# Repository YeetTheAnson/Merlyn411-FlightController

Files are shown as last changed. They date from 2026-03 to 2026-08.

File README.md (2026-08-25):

# Merlyn411 Flight Controller

> [!TIP]
> The Merlyn411 is outdated! Check out the [Merlyn435](https://github.com/YeetTheAnson/Merlyn435-Flight-Stack/) for a more powerful and modern flight controller + ESC.

## Introduction

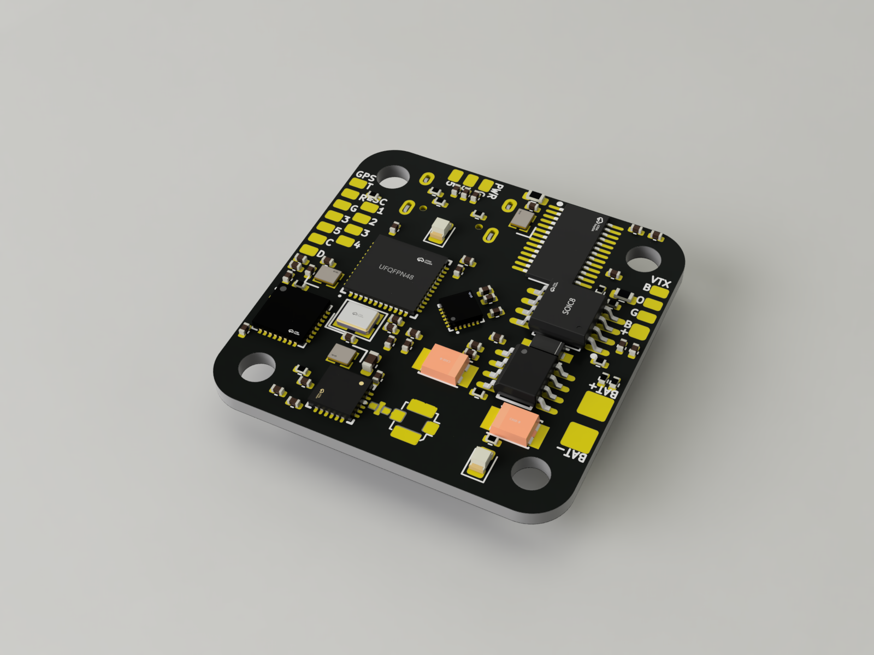
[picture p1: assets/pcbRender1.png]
render

This is my custom AIO (No ESC) flight controller! I started this project because commercial flight controllers get very expensive very quickly as you demand for more features like integrated radio receivers. I took on the challenge of designing my own betaflight compatible flight controller and it was difficult especially since the board has only 2 layers to save as much cost as possible and it's also my first time working with RF in circuits.

This flight controller is designed for a wide range of drones from 2" to as big as you want it to, and supports battery voltage from 2s to 8s although it is recommended to use a maximum of 6s. The 25.5mm pattern should be compatible with almost all frames on the market

It also features many quality of life features like an integrated ExpressLRS (ELRS) 2.4GHz receiver, an onboard OSD which inserts telemetry directly into the FPV video feed, 16MB flash memory for flight & blackbox logging and a buzzer for identifying error codes and to locate the drone.

While the primary focus of this projet is the flight controller hardware and firmware, I have also included a guide for the full 3 inch long range / freestyle drone build that this board was designed for

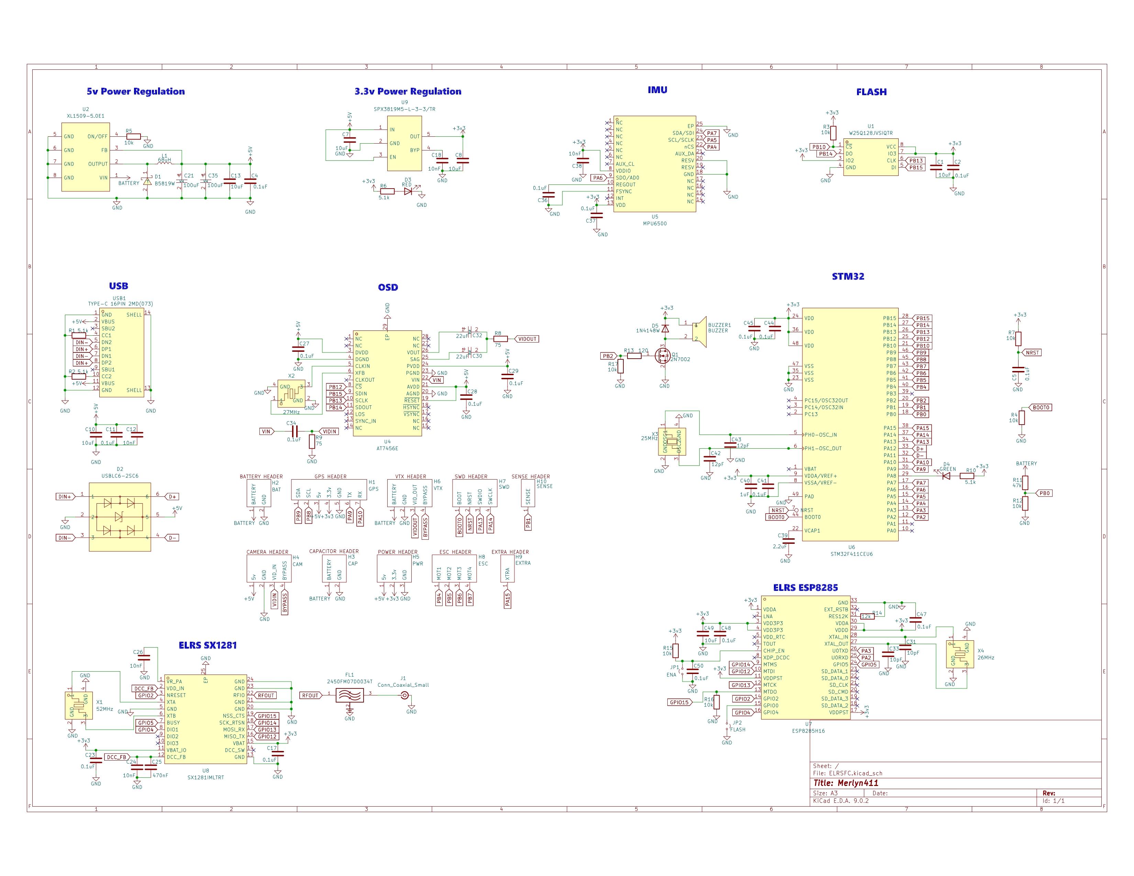
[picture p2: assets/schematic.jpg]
schematic

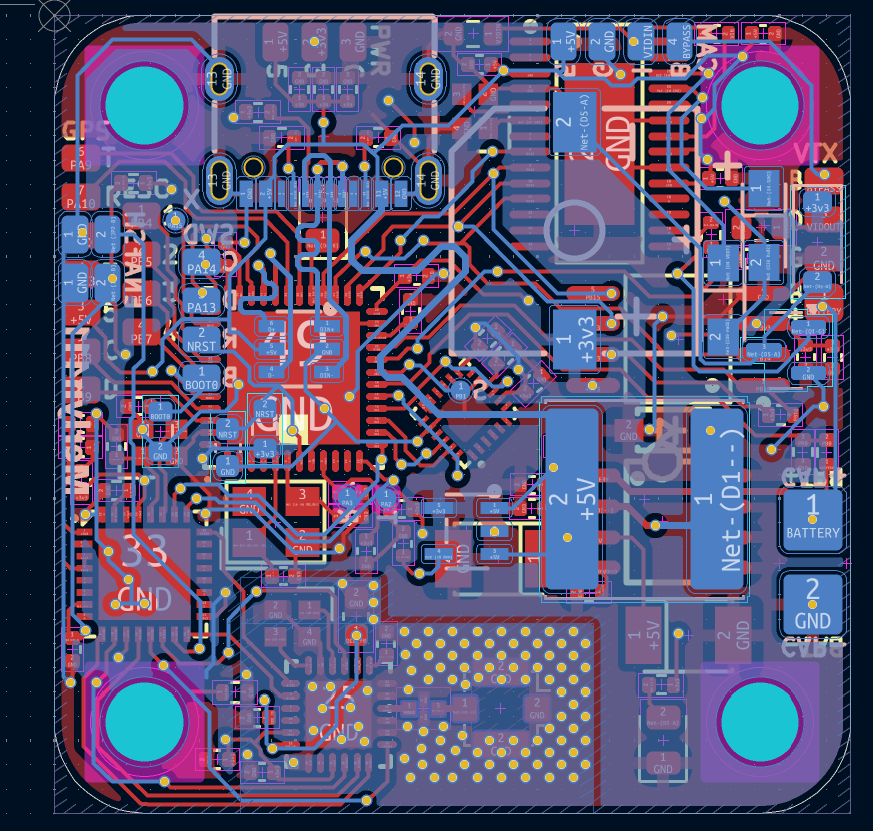
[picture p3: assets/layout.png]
layout

-----

## Hardware Specifications

  - **MCU:** STM32F411CEU6 (100MHz, 512KB Flash)
  - **IMU:** MPU6500 (SPI)
  - **OSD:** AT7456E (SPI)
  - **Blackbox:** Winbond W25Q128 16MB Flash (SPI)
  - **Receiver:** Integrated 2.4GHz ExpressLRS (ESP8285 & SX1281)
  - **Power Supply:** 5v and 3.3v rails up to 1A (3.3v rail is limited to 250mA)
  - **Mounting:** 25.5mm x 25.5mm square mounting pattern with M3 holes
  - **Peripherals** Includes pads for using external receivers, GPS, Magnetometer, analog camera and VTX

Note: The IMU should be in the forward facing direction if the USB C connector is facing forward and to the right. Adjust the mounting orientation accordingly in betaflight

-----

## Pinout
### External Headers

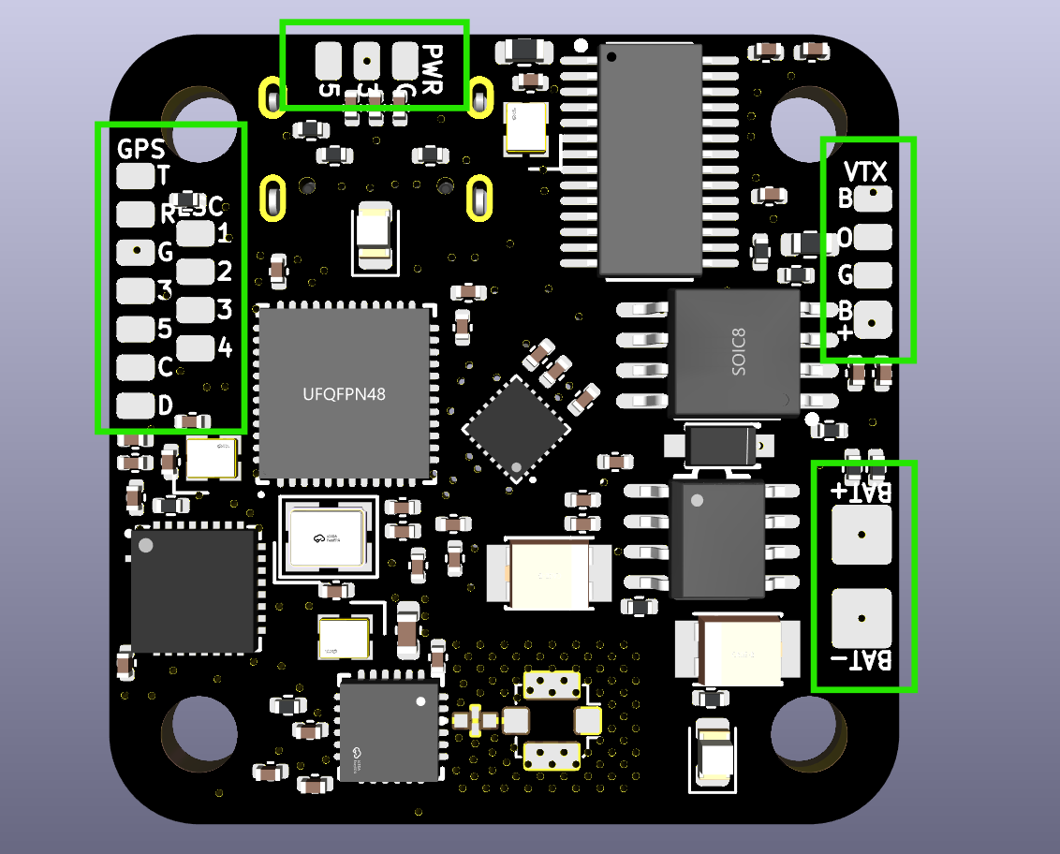
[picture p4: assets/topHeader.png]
topHeaders

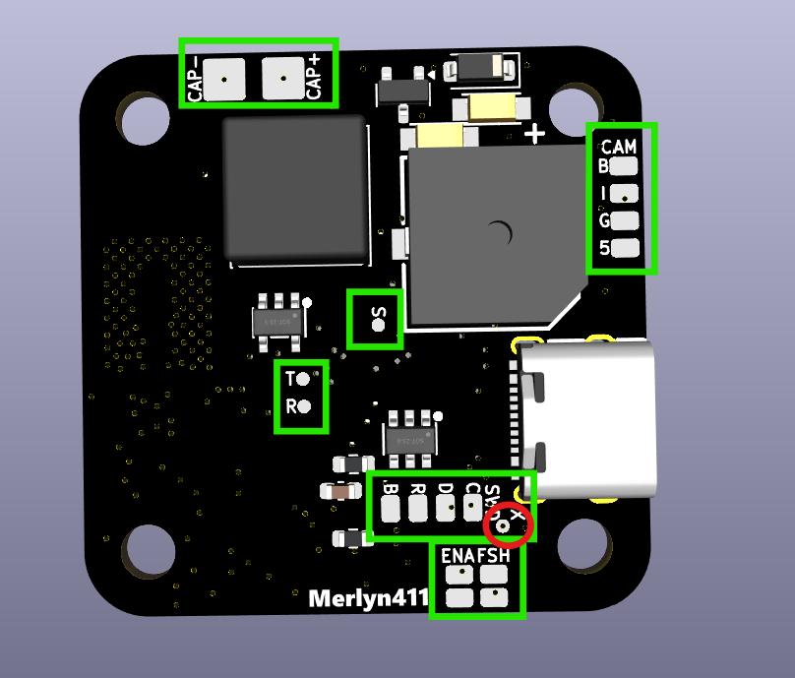
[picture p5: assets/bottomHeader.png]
bottomHeaders


| Header | Pin Name | STM32 Pin | Description |
| :--- | :--- | :--- | :--- |
| **GPS** | `T` | PA9 | UART1 TX (Connect to GPS RX) |
| | `R` | PA10 | UART1 RX (Connect to GPS TX) |
| | `3` | - | 3.3V Power Out |
| | `5` | - | 5V Power out |
| | `G` | - | Ground |
| | `C` | PB8 | I2C1 SCL (For Magnetometer) |
| | `D` | PB9 | I2C1 SDA (For Magnetometer) |
| **VTX** | `B`| - | Video Bypass (Direct from camera) |
| | `O` | - | Analog Video Out (From AT7456E) |
| | `G` | - | Ground |
| | `B+` | - | Battery Output |
| **CAM** | `B` | - | Video Bypass (Direct to VTX) |
| | `I` | - | Analog Video Input (From camera) |
| | `G` | - | Ground |
| | `5` | - | 5V Power Out |
| **SWD** | `C` | PA14 | SWCLK (Debug & Flash) |
| | `D` | PA13 | SWDIO (Debug & Flash) |
| | `R` | NRST | NRST (Debug & Flash) |
| | `B` | BOOT0 | BOOT0 (Debug & Flash) |
| **ESC** | `1-4` | PB4-PB7 | Motor Signal Outputs |
| **BAT** | `BAT+` | - | Battery Positive Input |
| | `BAT-` | - | Battery Negative Input |
| **CAP** | `CAP+` | - | Capacitor Anode |
| | `CAP-` | - | Capacitor Cathode |
| **PWR** | `G` | - | Ground |
| | `3` | - | 3.3V Power Out |
| | `5` | - | 5V Power Out |
| **Test Points** | `X` | PA15 | SmartAudio (Softserial 1 TX) |
| | `S` | PA15 | Current Sense Pin (From ESC) |
| | `T` | PA2 | ESP8285 RX Pin (STM32 TX PIN) |
| | `R` | PA3 | ESP8285 TX Pin (STM32 RX PIN) |

### Test Points & Pads

  - **External RX:**. Use these if you disable the internal ELRS receiver to connect other modules. Pad is labelled T and R on silkscreen.
  - **IRC Tramp and SmartAudio:** Connect VTX IRC or SmartAudio pin to the pad labeled with X on the silkscreen
  - **Current Sense:** Connect to ESC current sense pin. Pad is labelled S on silkscreen
  - **ENA & FSH:** Bridge ENA jumper to disable internal ELRS receiver. Bridge FSH jumper to put internal ELRS to flashing mode.
  - **Boot Mode (STM32):** To enter DFU mode for the flight controller, short the SWD B pad to any +3.3v rail while plugging in the USB.

-----

## Flight Controller Firmware (Betaflight)

Because this is a custom hardware layout, I believe that there is no standard targets that has the exact pin mapping as my flight controller. You must compile the firmware with the custom target definition in [/firmware/MERLYN411](https://github.com/YeetTheAnson/Merlyn411-FlightController/tree/main/firmware/MERLYN411) or use the pre compiled firmware in [/firmware/COMPILED](https://github.com/YeetTheAnson/Merlyn411-FlightController/tree/main/firmware/COMPILED).

> [!TIP]
> You can use flash another target to the flight controller and use betaflight CLI to remap the pin resource, however this is not recommended as the chosen target might not be compiled with a feature that this flight controller supports.

### How to build the firmware

1. Clone the [betaflight repository](https://github.com/betaflight/betaflight) using any UNIX terminal (use MYSYS2 MINGW64 on windows) and enter the directory
2. Enter `make configs` (install any required GCC toolchain if required)
3. Create a directory in betaflight/src/config/configs named `MERLYN411` and paste [config.h](https://github.com/YeetTheAnson/Merlyn411-FlightController/tree/main/firmware/MERLYN411/config.h) in the new directory
4. Enter `make MERLYN411` and the `.hex` file should appear in `betaflight/obj`

### Flashing the Flight Controller

1. **Via USB (DFU Mode):** Short the SWD `B` pad to 3.3v on the FC and plug in the USB C cable. Open Betaflight Configurator, select your compiled local `.hex` file, and click Flash Firmware.
2. **Via SWD:** If the bootloader is corrupted, connect an ST Link programmer to the `D`, `C`, and `D` (`R` is optional) pads and flash via STM32CubeProgrammer.

-----

## ExpressLRS Flashing

The internal ESP8285 and SX1281 receiver is wired to the STM32 via a hardware UART. It uses the standard **BETAFPV 2.4GHz Lite RX** firmware target. You can obtain the firmware binaries from the ELRS [site](https://expresslrs.github.io/web-flasher/) or from this repository in [/firmware/COMPILED](https://github.com/YeetTheAnson/Merlyn411-FlightController/tree/main/firmware/COMPILED). There's two way to flash the receiver:

### Method 1: Betaflight Passthrough

Note that betaflight must be installed and configured before passthrough works
1. Connect the FC via USB
2. Open the ExpressLRS Configurator [web flasher](https://expresslrs.github.io/web-flasher/) or app
3. Select `Receiver`
4. Select the `BETAFPV 2.4GHz Lite RX` target and press next
5. [OPTIONAL] Enter your bind phrase
6. Select the Betaflight Passthrough flashing method, press next and follow the steps

### Method 2: Manual Flashing

If the ESP8285 is bricked or passthrough fails, you can flash it directly using an FTDI adapter or another ESP8285/ESP8286/ESP32 or even an arduino

**Wiring the FTDI:**
The UART pads on the board are named relative to the STM32's perspective. Because the STM32's `TX` is connected to the ESP8285's `RX`, you must wire your FTDI adapter **RX to RX** and **TX to TX**.

  * FTDI `TX` -\> FC Pad `T`
  * FTDI `RX` -\> FC Pad `R`
  * FTDI `GND` -\> FC Pad `G`
  * FTDI `5V` -\> FC Pad `5` (or power via USB)

You must disable the STM32 when flashing via the T and R pad
using an external FTDI as it will intefere with the UART lines. You can disable the STM32 by shorting the SWD `R` pad to ground. Remember to short the `ENA` pads on the bottom side to put the ESP8285 into flashing mode.

-----

## Drone Assembly

While this project is mainly focused on the Merlyn411 flight controller, I designed it along with a high efficiency 3 inch cruiser drone in mind. If you want to recreate the full build, below is the component breakdown and assembly steps

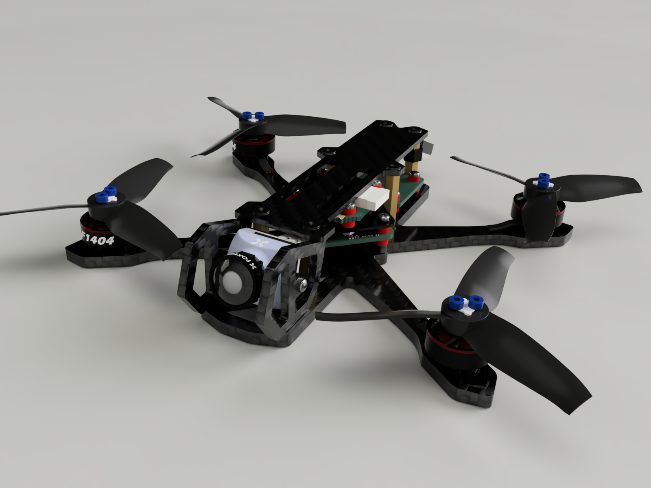
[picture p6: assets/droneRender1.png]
droneRender


### Component List
- **Flight Controller:** Merlyn411
- **ESC:** JHEMCU EM40A
- **Motors:** Sparkhobby 1303.5 5500KV
- **Propellers:** Gemfan 3016 Tri-Blade
- **VTX:** JHEMCU 600mW VTX
- **Camera:** Analog FPV micro(19mm) camera
- **Frame:** Custom frame
- **Battery:** 2S-4S LiPo or 2S/3S 18650 Li Ion packs

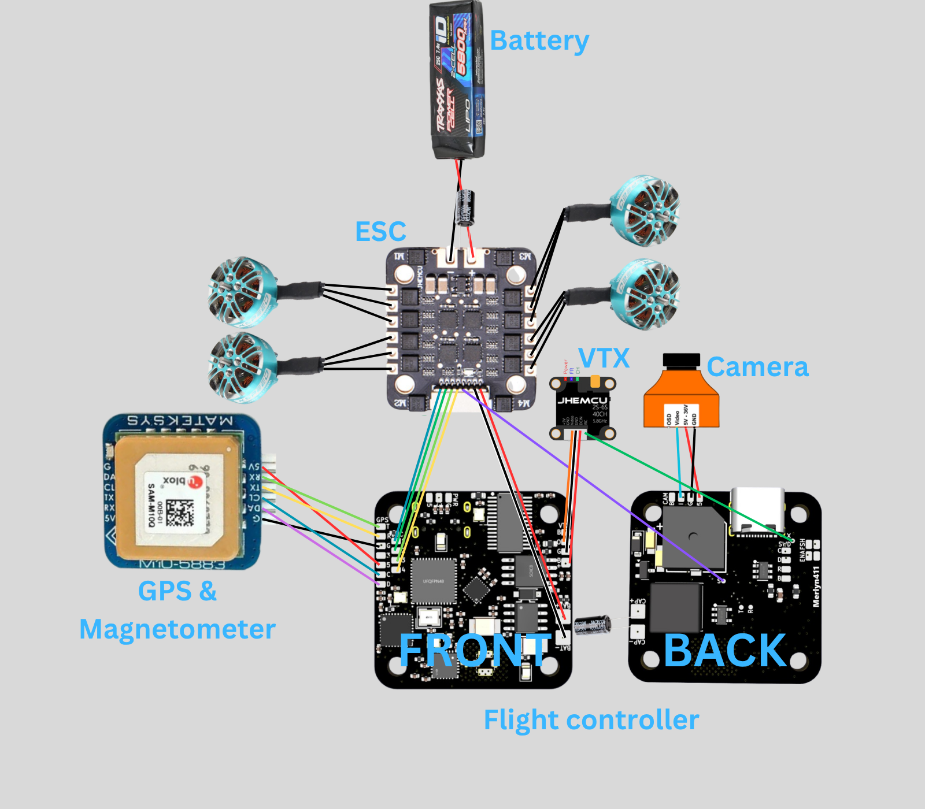
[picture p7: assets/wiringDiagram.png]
Wiring Diagram


### Why 3D Printing the Frame is Not Recommended
Currently, I am using a custom frame that I 3D printed for prototyping. I strongly advise against using a 3D printed frame for your final build. The Merlyn411 uses the MPU6500 IMU, which is sensitive to mechanical noise and vibrations. 3D printed frames will flex and resonate significantly more than carbon fiber frames. This flexing will send noise into the gyro and resulting in terrible flight performance. Also the 3D printed frame will likely not survive a moderate impact.

### Fasteners
Because this is a custom stack with a 25.5mm FC and a 20mm ESC, the stack up is very specific. You will need:
* 6x M3 20mm Female to Female Brass Standoffs (Frame separation)
* 12x M3 6mm Screws (Frame to standoffs)
* 4x M2 Nuts (Stack base)
* 4x M2 16mm Screws (Main stack skewers)
* 8x M2 10mm Screws (Top stack/VTX skewers)
* 16x M2 6mm Screws (Motors)
* 4x M2 6mm Screws (Camera/Props)

### FC Stack
The Merlyn411 uses a 25.5x25.5mm mounting pattern (which is meant for AIO boards). However, I needed a standalone ESC which comes in standard sizes like 20x20mm.

To make these fit together, you must use a 3D printed adapter plate in [/production/3dPrint/boardAdapter.stl](https://github.com/YeetTheAnson/Merlyn411-FlightController/blob/main/production/3dPrint/boardAdapter.stl). 

**Stack Assembly Layer 1:**
1.  Place 4x M2 Nuts into the designated recesses in the bottom frame plate.
2. Push rubber grommets into the flight controller
3. Push 4x M2 16mm screws through the adapter plate, through the rubber grommet, and through the bottom plate into the M2 nuts
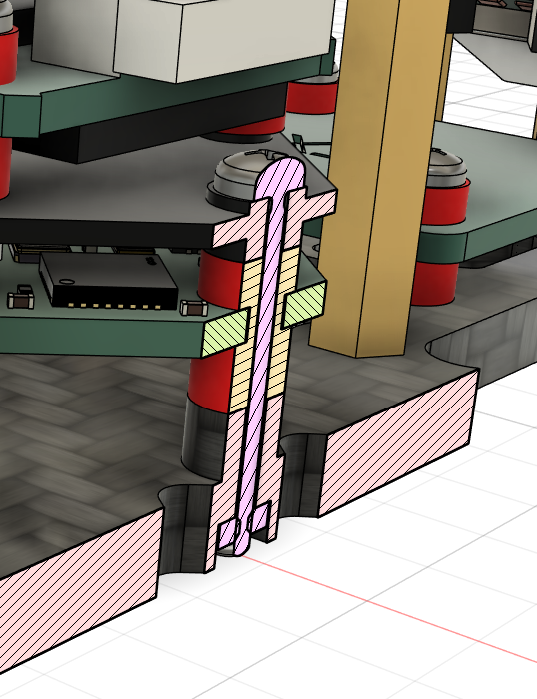
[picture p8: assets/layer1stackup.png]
layer1


**Stack Assembly Layer 2:**
1. Push rubber grommets into the ESC
2. Push 4x M2 10mm screws through rubber grommets and through the adapter plate until it reaches another set of M2 nuts
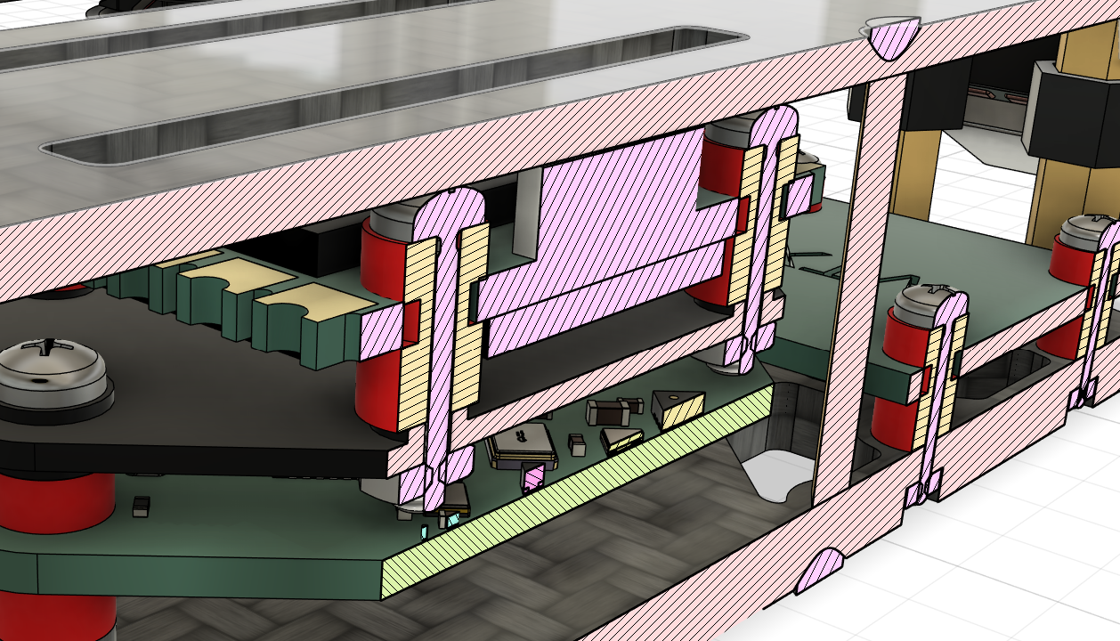
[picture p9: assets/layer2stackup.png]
layer2


### Mounting the VTX
The JHEMCU 600mW VTX mounts to the rear of the frame.
1.  Place 4x M2 Nuts into the bottom frame plate at in the rear
2. Push rubber grommets into the VTX
3.  Thread 4x M2 10mm screws through rubber grommets, down through the bottom plate, and into the nuts

### Final Assembly
1.  **Motors:** Mount the four 1303.5 5500KV motors to the arms using 16x M2 6mm screws (4 per motor). Ensure the screws do not touch the motor windings inside the bell.
2.  **Propellers:** Mount the Gemfan 3016 propeller. Pay attention to motor rotation directions (depending on your betaflight configuration, it could either be prop in or prop out). Fasten each prop with 2x M2 6mm screws.
3.  **Camera:** Mount the analog FPV camera to the front using 2x M2 6mm screws.
4.  **Closing the Frame:** Use the 6x M3 20mm standoffs and 12x M3 6mm screws to secure the top plate to the bottom plate

## Bill of Material
Note: The prices in USD are converted as of 31 March 2026 and prices may fluctuate. The requested funding is $200 as a buffer for the unstable prices. Any unused funds is returned.

| Item Name | Link | Vendor | Quantity | Total Price (USD) |
|---|---|---|---|---|
| 2450FM07D0034 | [Link](https://www.aliexpress.com/item/1005007939000699.html) | AliExpress | 1 | 6.40 |
| AliExpress Shipping |  | AliExpress | 1 | 3.15 |
| PCB |  | JLCPCB | 1 | 2.00 |
| PCB Assembly |  | JLCPCB | 1 | 79.49 |
| JLCPCB Shipping |  | JLCPCB | 1 | 6.02 |
| Sparkhobby 1303.5 5500KV motor | [Link](https://click.world.taobao.com/_b.QbWPiG) | Taobao | 4 | 22.50 |
| JHEMCU EM40A ESC | [Link](https://click.world.taobao.com/_b.ubW0U5) | Taobao | 1 | 18.11 |
| 19mm FPV Camera | [Link](https://click.world.taobao.com/_b.LbWPiH) | Taobao | 1 | 5.16 |
| JHEMCU 600mW VTX | [Link](https://click.world.taobao.com/_b.vbWPq7) | Taobao | 1 | 14.58 |
| M10 GPS & Magnetometer | [Link](https://click.world.taobao.com/_b.TbWPjE) | Taobao | 1 | 7.55 |
| Rubber Grommet Shock Mount | [Link](https://click.world.taobao.com/_b.XbWPTq) | Taobao | 12 | 0.80 |
| Gemfan 3016 | [Link](https://click.world.taobao.com/_b.4bW0jv) | Taobao | 1 | 1.75 |
| ELRS Dipole Antenna | [Link](https://click.world.taobao.com/_b.obW0UN) | Taobao | 1 | 0.90 |
| Taobao Tax |  | Taobao | 1 | 8.35 |
| Taobao Shipping |  | Taobao | 1 | 2.48 |
| 10k Resistor | [Link](https://shopee.com.my/100PCS-0603-1-SMD-Resistor-1.1K-~-100K-2K-10K-15K-20K-30K-51K-62K-75K-100K-Patch-resistance-i.1135937572.18786797162) | Shopee | 1 | 0.45 |
| 100nF Capacior | [Link](https://shopee.com.my/100PCS-0603-SMD-Chip-Multilayer-Ceramic-Capacitor-330PF-22uF-1nF-10nF-15nF-100nF-0.1uF-1uF-2.2uF-4.7uF-10uF-i.1135937572.21395687476) | Shopee | 1 | 0.45 |
| 22uF Tantalum | [Link](https://shopee.com.my/10PCS-A-Type-Tantalum-Capacitor-100uf-150uf-220uf-330uf-470uf-680uf-6V-6.3V-10V-16V-25V-35V-50V-4.7-6.8-10-15-22-33-47uf-i.1135937572.217956874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) | Shopee | 1 | 0.88 |
| USBCL6-2SC6 | [Link](https://shopee.com.my/50Pcs-5pcs-USBLC-USBLC6-2SC6-SOT-23-6-USBLC6-SOT-UL26-SOT23-Low-Capacitor-Capacitance-2-wire-ESD-Static-Protection-Chip-IC-i.1649836180.4192388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) | Shopee | 1 | 0.83 |
| 2N7002LT | [Link](https://shopee.com.my/2N7002LT-2N7002-7002-N-Channel-MOSFET-N-CH-SOT23-SMD-IC-MOS-FET-Field-Effect-Tube-SOT-23-i.1649836180.44952514481) | Shopee | 1 | 0.79 |
| 9650 Active Buzzer | [Link](https://shopee.com.my/SMD-Buzzer-9018-9025-9045-1109-9650-3V-5V-Magnetic-Mini-Active-Passive-Piezo-Buzzers-Loudspeaker-Loud-Beep-Alarm-For-Arduino-i.1649836180.46152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) | Shopee | 1 | 1.05 |
| SPX3819 | [Link](https://shopee.com.my/10pcs-5pcs-SPX3819-SPX3819M5-L-3-3-TR-SOT-23-5-SPX3819M5-3.3-SPX3819M5-3-3-TR-SOT23-3.3V-500mA-Regulator-LDO-IC-New-Original-i.1649836180.50452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) | Shopee | 1 | 1.45 |
| 8040 68uH Inductor | [Link](https://shopee.com.my/10pcs-4030-SWPA4030S-4020-5040-6045-8040-SMD-Power-Inductor-2.2uH-3.3uH-4.7uH-6.8uH-10uH-15uH-22uH-33uH-47uH-56uH-Wire-Wound-i.1649836180.55202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) | Shopee | 1 | 1.51 |
| SPX Express Shipping |  | Shopee | 2 | 2.56 |
| **GRAND TOTAL** |  |  |  | **189.21** |

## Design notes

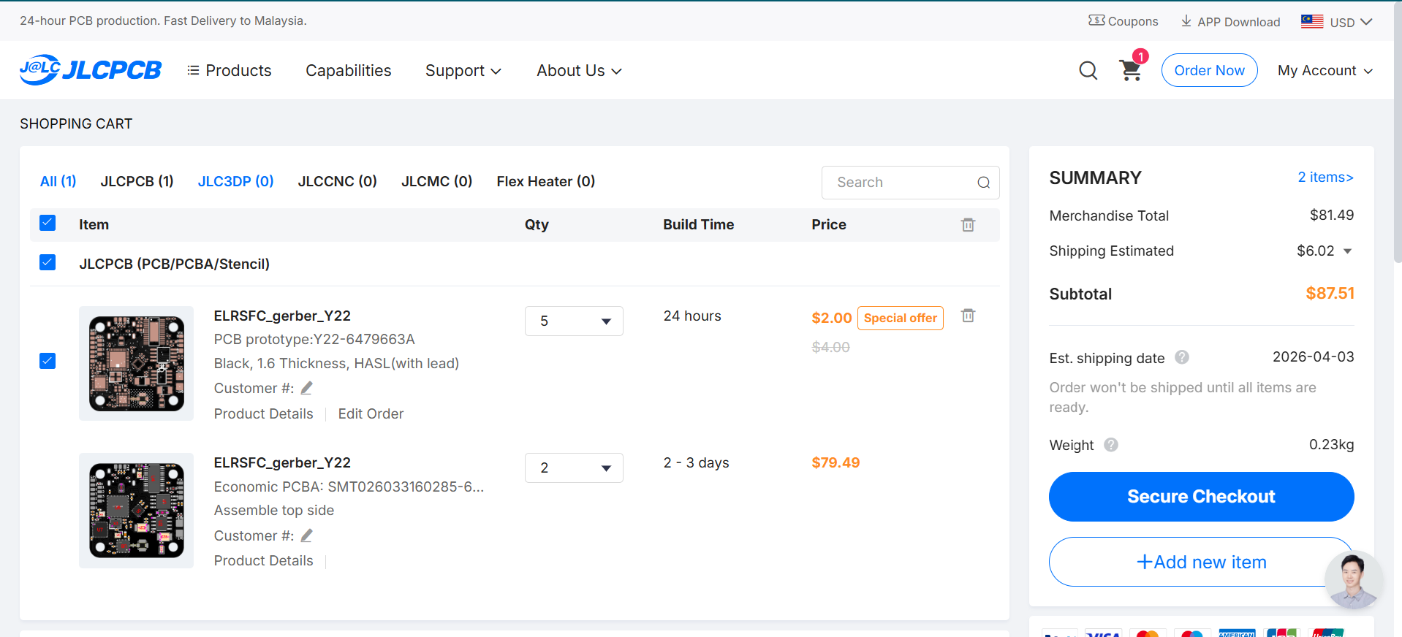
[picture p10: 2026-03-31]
cartScreenshots/jlcCart.png

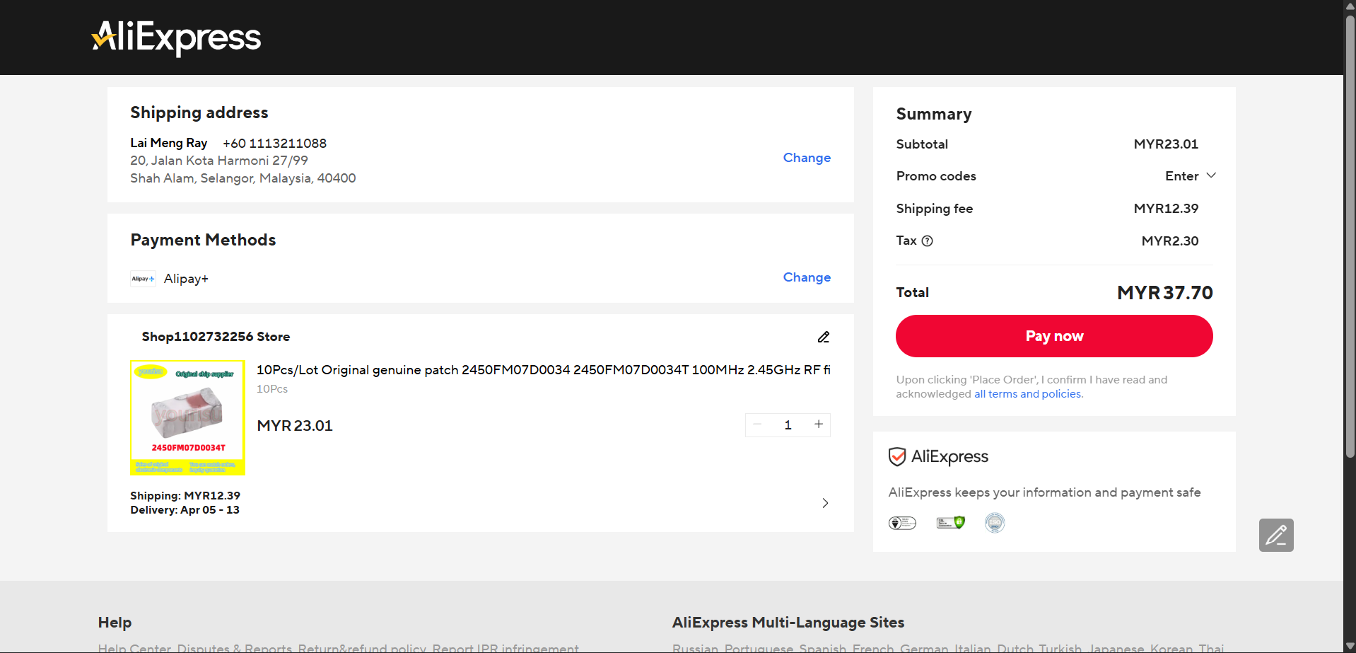
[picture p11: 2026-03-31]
cartScreenshots/alieCheckout.png

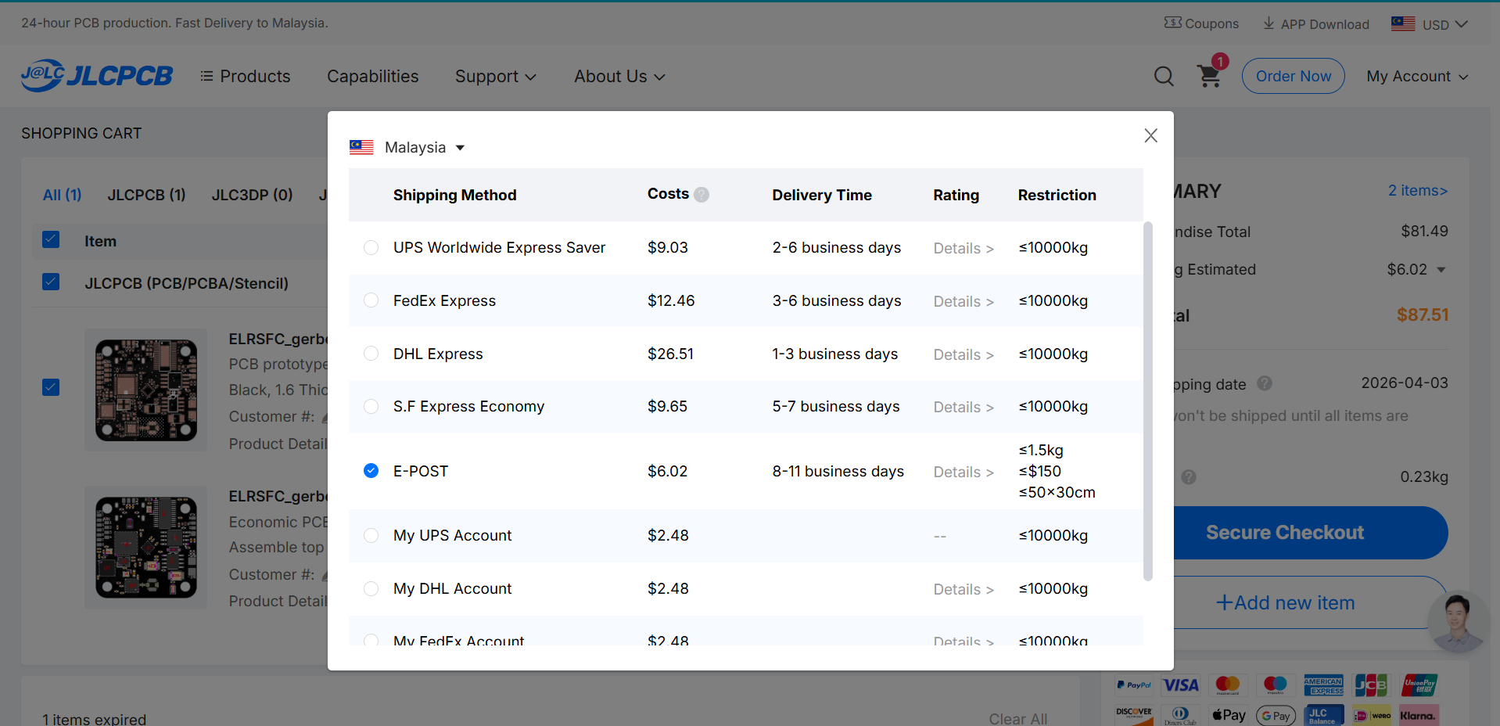
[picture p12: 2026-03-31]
cartScreenshots/jlcShipping.png

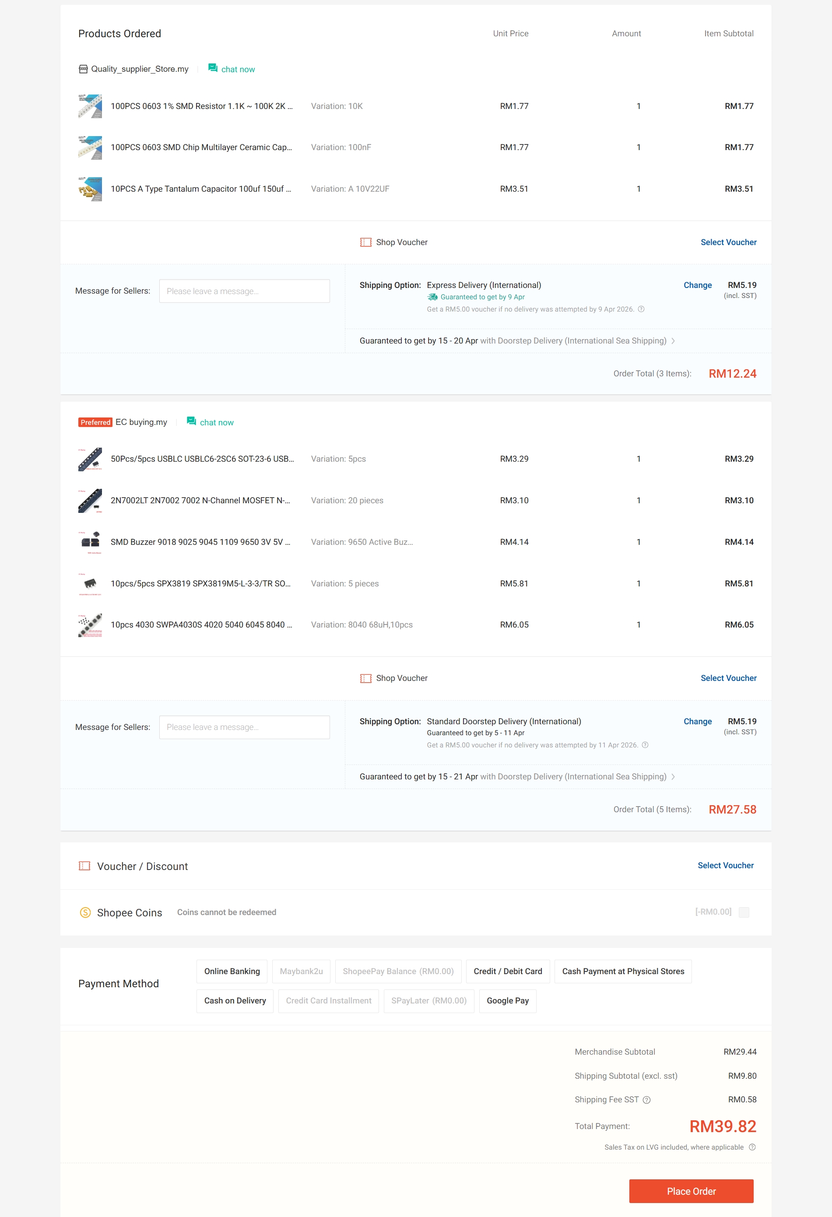
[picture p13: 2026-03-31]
cartScreenshots/shopeeCheckout.jpeg

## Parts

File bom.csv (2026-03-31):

Item Name | Link | Vendor | Quantity | Total Price (USD)
2450FM07D0034 | https://www.aliexpress.com/item/1005007939000699.html | AliExpress | 1 | 6.40
AliExpress Shipping |  | AliExpress | 1 | 3.15
PCB |  | JLCPCB | 1 | 2.00
PCB Assembly |  | JLCPCB | 1 | 79.49
JLCPCB Shipping |  | JLCPCB | 1 | 6.02
Sparkhobby 1303.5 5500KV motor | https://click.world.taobao.com/_b.QbWPiG | Taobao | 4 | 22.50
JHEMCU EM40A ESC | https://click.world.taobao.com/_b.ubW0U5 | Taobao | 1 | 18.11
19mm FPV Camera | https://click.world.taobao.com/_b.LbWPiH | Taobao | 1 | 5.16
JHEMCU 600mW VTX | https://click.world.taobao.com/_b.vbWPq7 | Taobao | 1 | 14.58
M10 GPS & Magnetometer | https://click.world.taobao.com/_b.TbWPjE | Taobao | 1 | 7.55
Rubber Grommet Shock Mount | https://click.world.taobao.com/_b.XbWPTq | Taobao | 12 | 0.80
Gemfan 3016 | https://click.world.taobao.com/_b.4bW0jv | Taobao | 1 | 1.75
ELRS Dipole Antenna | https://click.world.taobao.com/_b.obW0UN | Taobao | 1 | 0.90
Taobao Tax |  | Taobao | 1 | 8.35
Taobao Shipping |  | Taobao | 1 | 2.48
10k Resistor | https://shopee.com.my/100PCS-0603-1-SMD-Resistor-1.1K-~-100K-2K-10K-15K-20K-30K-51K-62K-75K-100K-Patch-resistance-i.1135937572.18786797162 | Shopee | 1 | 0.45
100nF Capacior | https://shopee.com.my/100PCS-0603-SMD-Chip-Multilayer-Ceramic-Capacitor-330PF-22uF-1nF-10nF-15nF-100nF-0.1uF-1uF-2.2uF-4.7uF-10uF-i.1135937572.21395687476 | Shopee | 1 | 0.45
22uF Tantalum | https://shopee.com.my/10PCS-A-Type-Tantalum-Capacitor-100uf-150uf-220uf-330uf-470uf-680uf-6V-6.3V-10V-16V-25V-35V-50V-4.7-6.8-10-15-22-33-47uf-i.1135937572.21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 | Shopee | 1 | 0.88
USBCL6-2SC6 | https://shopee.com.my/50Pcs-5pcs-USBLC-USBLC6-2SC6-SOT-23-6-USBLC6-SOT-UL26-SOT23-Low-Capacitor-Capacitance-2-wire-ESD-Static-Protection-Chip-IC-i.1649836180.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 | Shopee | 1 | 0.83
2N7002LT | https://shopee.com.my/2N7002LT-2N7002-7002-N-Channel-MOSFET-N-CH-SOT23-SMD-IC-MOS-FET-Field-Effect-Tube-SOT-23-i.1649836180.44952514481 | Shopee | 1 | 0.79
9650 Active Buzzer | https://shopee.com.my/SMD-Buzzer-9018-9025-9045-1109-9650-3V-5V-Magnetic-Mini-Active-Passive-Piezo-Buzzers-Loudspeaker-Loud-Beep-Alarm-For-Arduino-i.164983618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 | Shopee | 1 | 1.05
SPX3819 | https://shopee.com.my/10pcs-5pcs-SPX3819-SPX3819M5-L-3-3-TR-SOT-23-5-SPX3819M5-3.3-SPX3819M5-3-3-TR-SOT23-3.3V-500mA-Regulator-LDO-IC-New-Original-i.164983618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 | Shopee | 1 | 1.45
8040 68uH Inductor | https://shopee.com.my/10pcs-4030-SWPA4030S-4020-5040-6045-8040-SMD-Power-Inductor-2.2uH-3.3uH-4.7uH-6.8uH-10uH-15uH-22uH-33uH-47uH-56uH-Wire-Wound-i.164983618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 | Shopee | 1 | 1.51
SPX Express Shipping |  | Shopee | 2 | 2.56
GRAND TOTAL |  |  |  | 189.21

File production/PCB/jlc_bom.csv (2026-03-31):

Designator | Footprint | Quantity | Value | LCSC Part #
BUZZER1 | BUZ-SMD_L9.6-W9.6-LS10.0-R | 1 | BUZZER | C96127
C1, C10, C13, C49, C7, C8 | 0402 | 6 | 10uF | C15525
C11, C17, C2, C23, C27, C28, C29, C34, C36, C37, C4, C41, C44, C45, C47, C48, C50 | 0402 | 17 | 0.1uF | C307331
C12, C18, C24, C26, C38 | 0402 | 5 | 10nF | C15195
C21, C35 | CASE-B_3528 | 2 | 100uF | C16133
C25 | 0603 | 1 | 470nF | C1623
C30, C32 | CAP-SMD_L3.2-W1.6-RD-C7171 | 2 | 22uF
C31, C33 | 0402 | 2 | 10pF | C32949
C39 | 0402 | 1 | 2.2uF | C12530
C40 | 0402 | 1 | 1uF | C52923
C42, C43 | 0402 | 2 | 12pF | C1547
C5 | 0603 | 1 | 0.1uF
D1 | SOD-123_L2.7-W1.6-LS3.7-RD-1 | 1 | B5819W | C8598
D2 | SOT-23-6_L2.9-W1.6-P0.95-LS2.8-BL | 1 | USBLC6-2SC6 | C7519
D3 | 0805 | 1 | RED | C84256
D4 | 0805 | 1 | GREEN | C2297
D5 | D_SOD-123 | 1 | 1N4148W
FL1 | FIL_2450FM07D0034T | 1 | 2450FM07D0034T
H1 | GPS | 1 | GPS
H10 | SENSE | 1 | SENSE
H2 | BAT | 1 | BAT
H3 | CAP | 1 | CAP
H4 | CAM | 1 | CAM
H5 | PWR | 1 | PWR
H6 | VTX | 1 | VTX
H7 | SWD | 1 | SWD
H8 | ESC | 1 | ESC
H9 | EXTRA | 1 | EXTRA
J1 | UFL | 1 | Conn_Coaxial_Small
JP1 | ENA | 1 | ENA
JP2 | FLASH | 1 | FLASH
L1 | L_Sunlord_SWPA8040S | 1 | 68uH
Q1 | SOT-23 | 1 | 2N7002
R1, R10, R2, R6 | 0402 | 4 | 5.1k | C25905
R11 | 0402 | 1 | 47k | C25792
R12, R15, R16, R17, R3, R5 | 0402 | 6 | 10k | C25744
R13 | 0402 | 1 | 120 | C25079
R14 | 0402 | 1 | 12k | C25752
R4, R7 | 0603 | 2 | 10k
R8, R9 | 0603 | 2 | 75 | C4275
U1 | SOIC-8_L5.3-W5.3-P1.27-LS8.0-BL | 1 | W25Q128JVSIQTR | C97521
U2 | SOIC-8_L5.0-W4.0-P1.27-LS6.0-BL | 1 | XL1509-5.0E1 | C61063
U4 | TSSOP-28_L9.7-W4.4-P0.65-LS6.4-BL-EP-2 | 1 | AT7456E | C82351
U5 | QFN-24_L3.0-W3.0-P0.40-BL-EP | 1 | MPU6500 | C50278
U6 | UFQFPN-48_L7.0-W7.0-P0.50-BL-EP | 1 | STM32F411CEU6 | C60420
U7 | QFN-32_L5.0-W5.0-P0.50-TL-EP3.7 | 1 | ESP8285H16 | C967019
U8 | QFN-24_L4.0-W4.0-P0.50-TL-EP2.6 | 1 | SX1281IMLTRT | C2151551
U9 | SOT-23-5_L3.0-W1.7-P0.95-LS2.8-BL | 1 | SPX3819M5-L-3-3/TR | C9055
USB1 | USB-C-SMD_TYPE-C-6PIN-2MD-073 | 1 | TYPE-C 16PIN 2MD(073) | C2765186
X1 | CRYSTAL-SMD_4P-L2.0-W1.6-BL | 1 | 52MHz | C3034316
X2 | CRYSTAL-SMD_4P-L2.0-W1.6-BL | 1 | 27MHz | C648952
X3 | CRYSTAL-SMD_4P-L3.2-W2.5-BL | 1 | 25MHz | C9006
X4 | CRYSTAL-SMD_4P-L2.0-W1.6-BL | 1 | 26MHz | C19272774

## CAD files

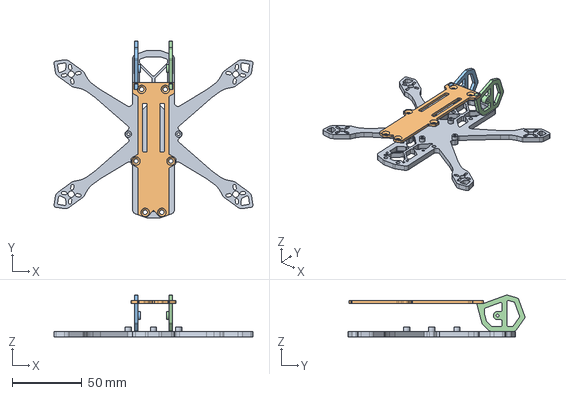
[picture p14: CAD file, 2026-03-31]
CAD/MerlynFPVFrame.step
142.7 x 126.8 x 30.0 mm

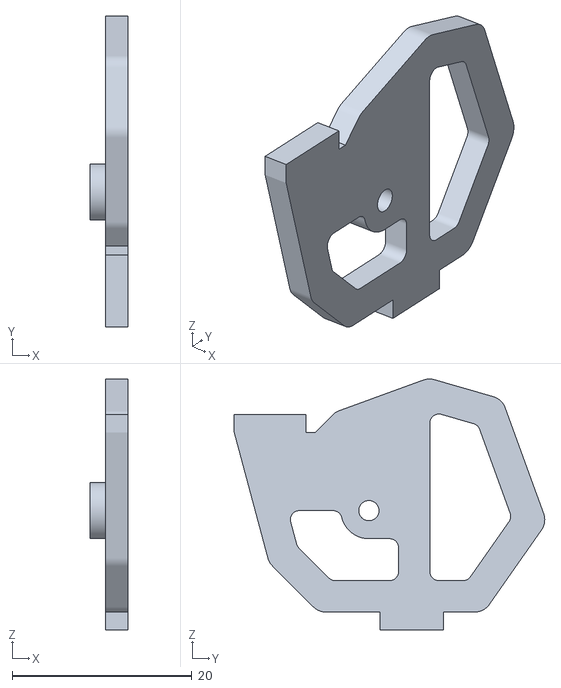
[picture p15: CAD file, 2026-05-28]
production/3dPrint/rightCameraFrameReinforced.stl
4.25 x 34.6 x 28.0

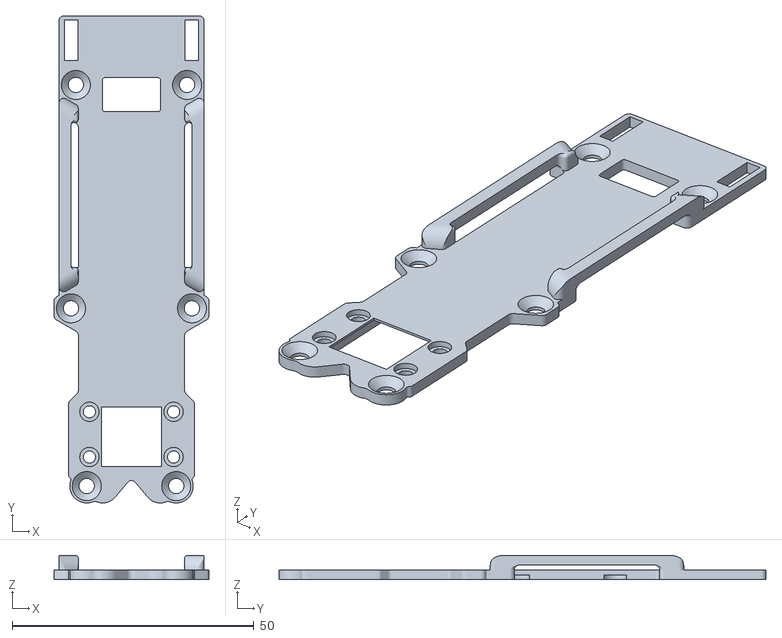
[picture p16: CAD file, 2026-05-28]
production/3dPrint/topFrameReinforced.stl
32.0 x 100.7 x 5.00

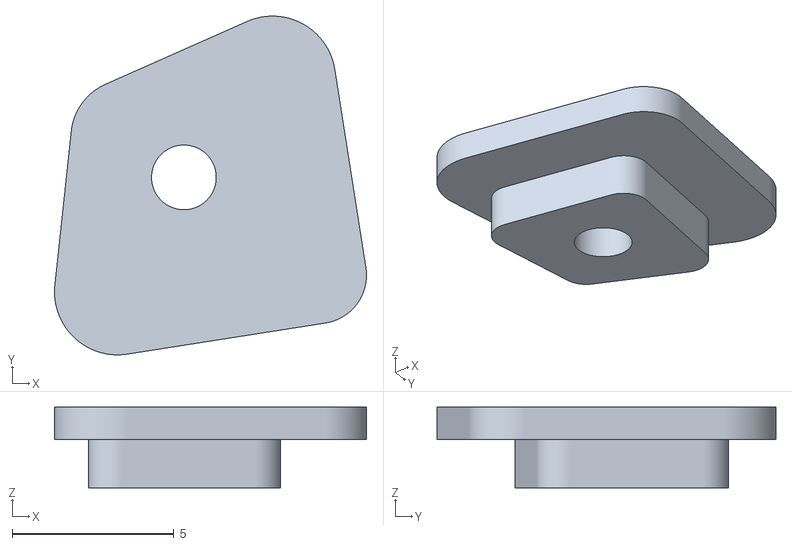
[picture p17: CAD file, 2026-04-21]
production/3dPrint/landingOnlyLock.stl
9.65 x 10.5 x 2.50

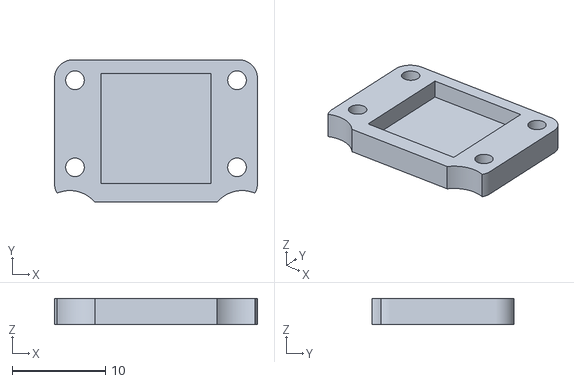
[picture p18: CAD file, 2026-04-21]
production/3dPrint/gpsLock.stl
21.8 x 15.3 x 2.80

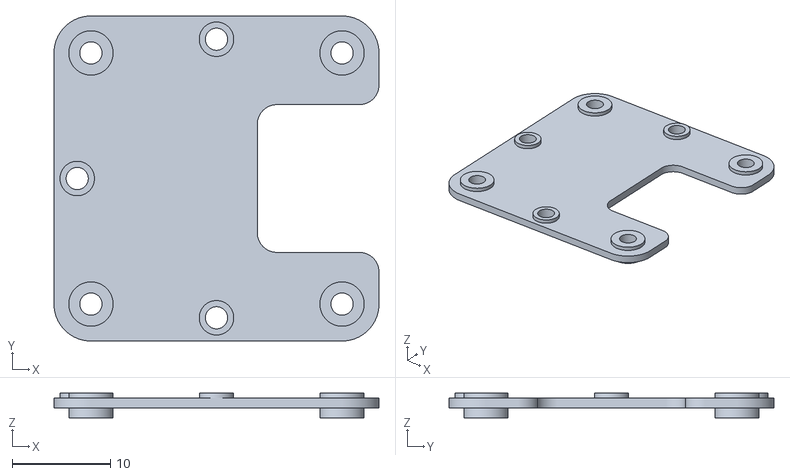
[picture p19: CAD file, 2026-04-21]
production/3dPrint/boardAdapter.stl
33.0 x 33.0 x 2.50

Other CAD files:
production/3dPrint/leftCameraFrameReinforced.stl
CAD/MerlynFPVFrame.f3d

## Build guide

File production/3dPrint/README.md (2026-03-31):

Note that CAD files is in /CAD directory

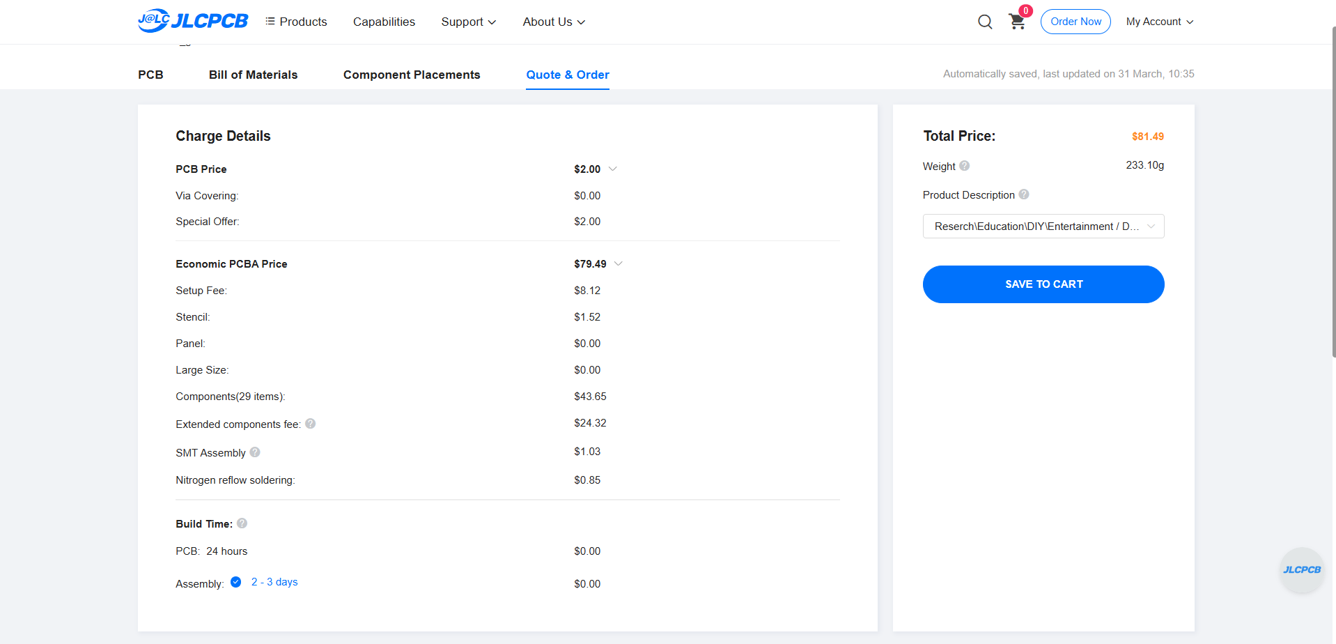
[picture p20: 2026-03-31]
cartScreenshots/jlcAssembly.png

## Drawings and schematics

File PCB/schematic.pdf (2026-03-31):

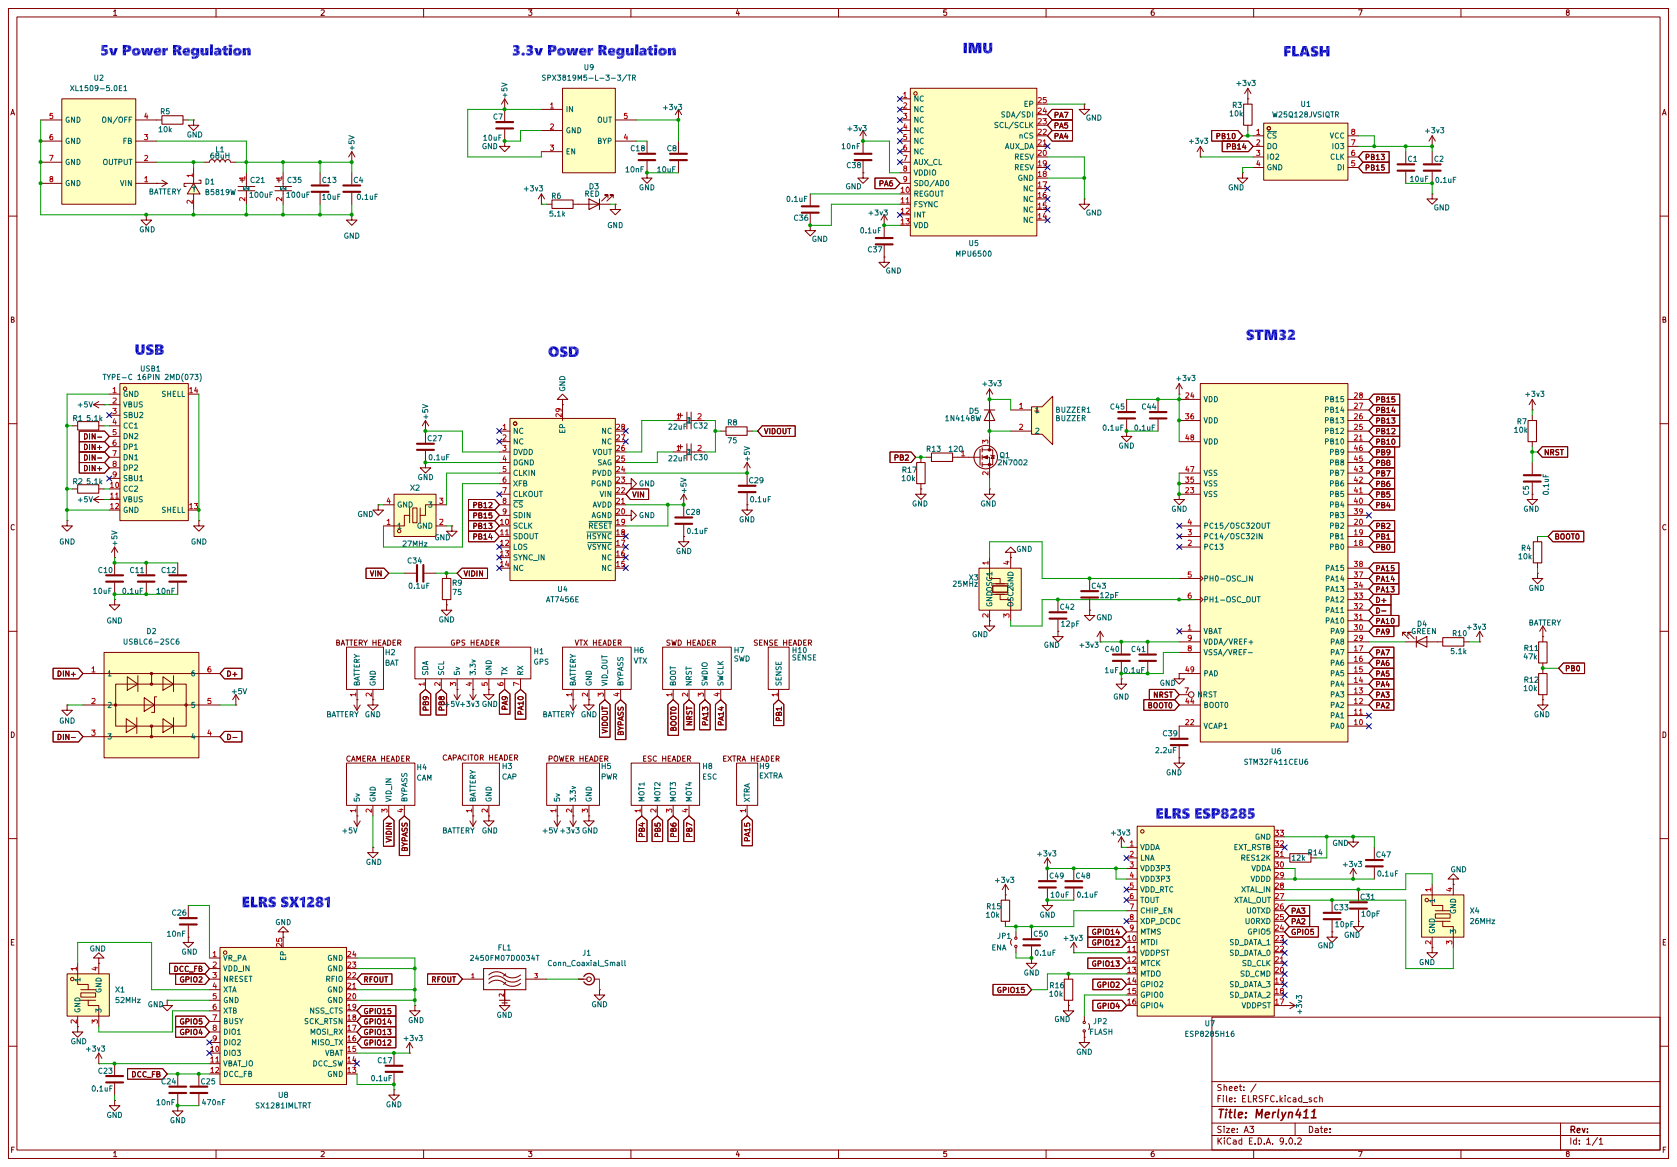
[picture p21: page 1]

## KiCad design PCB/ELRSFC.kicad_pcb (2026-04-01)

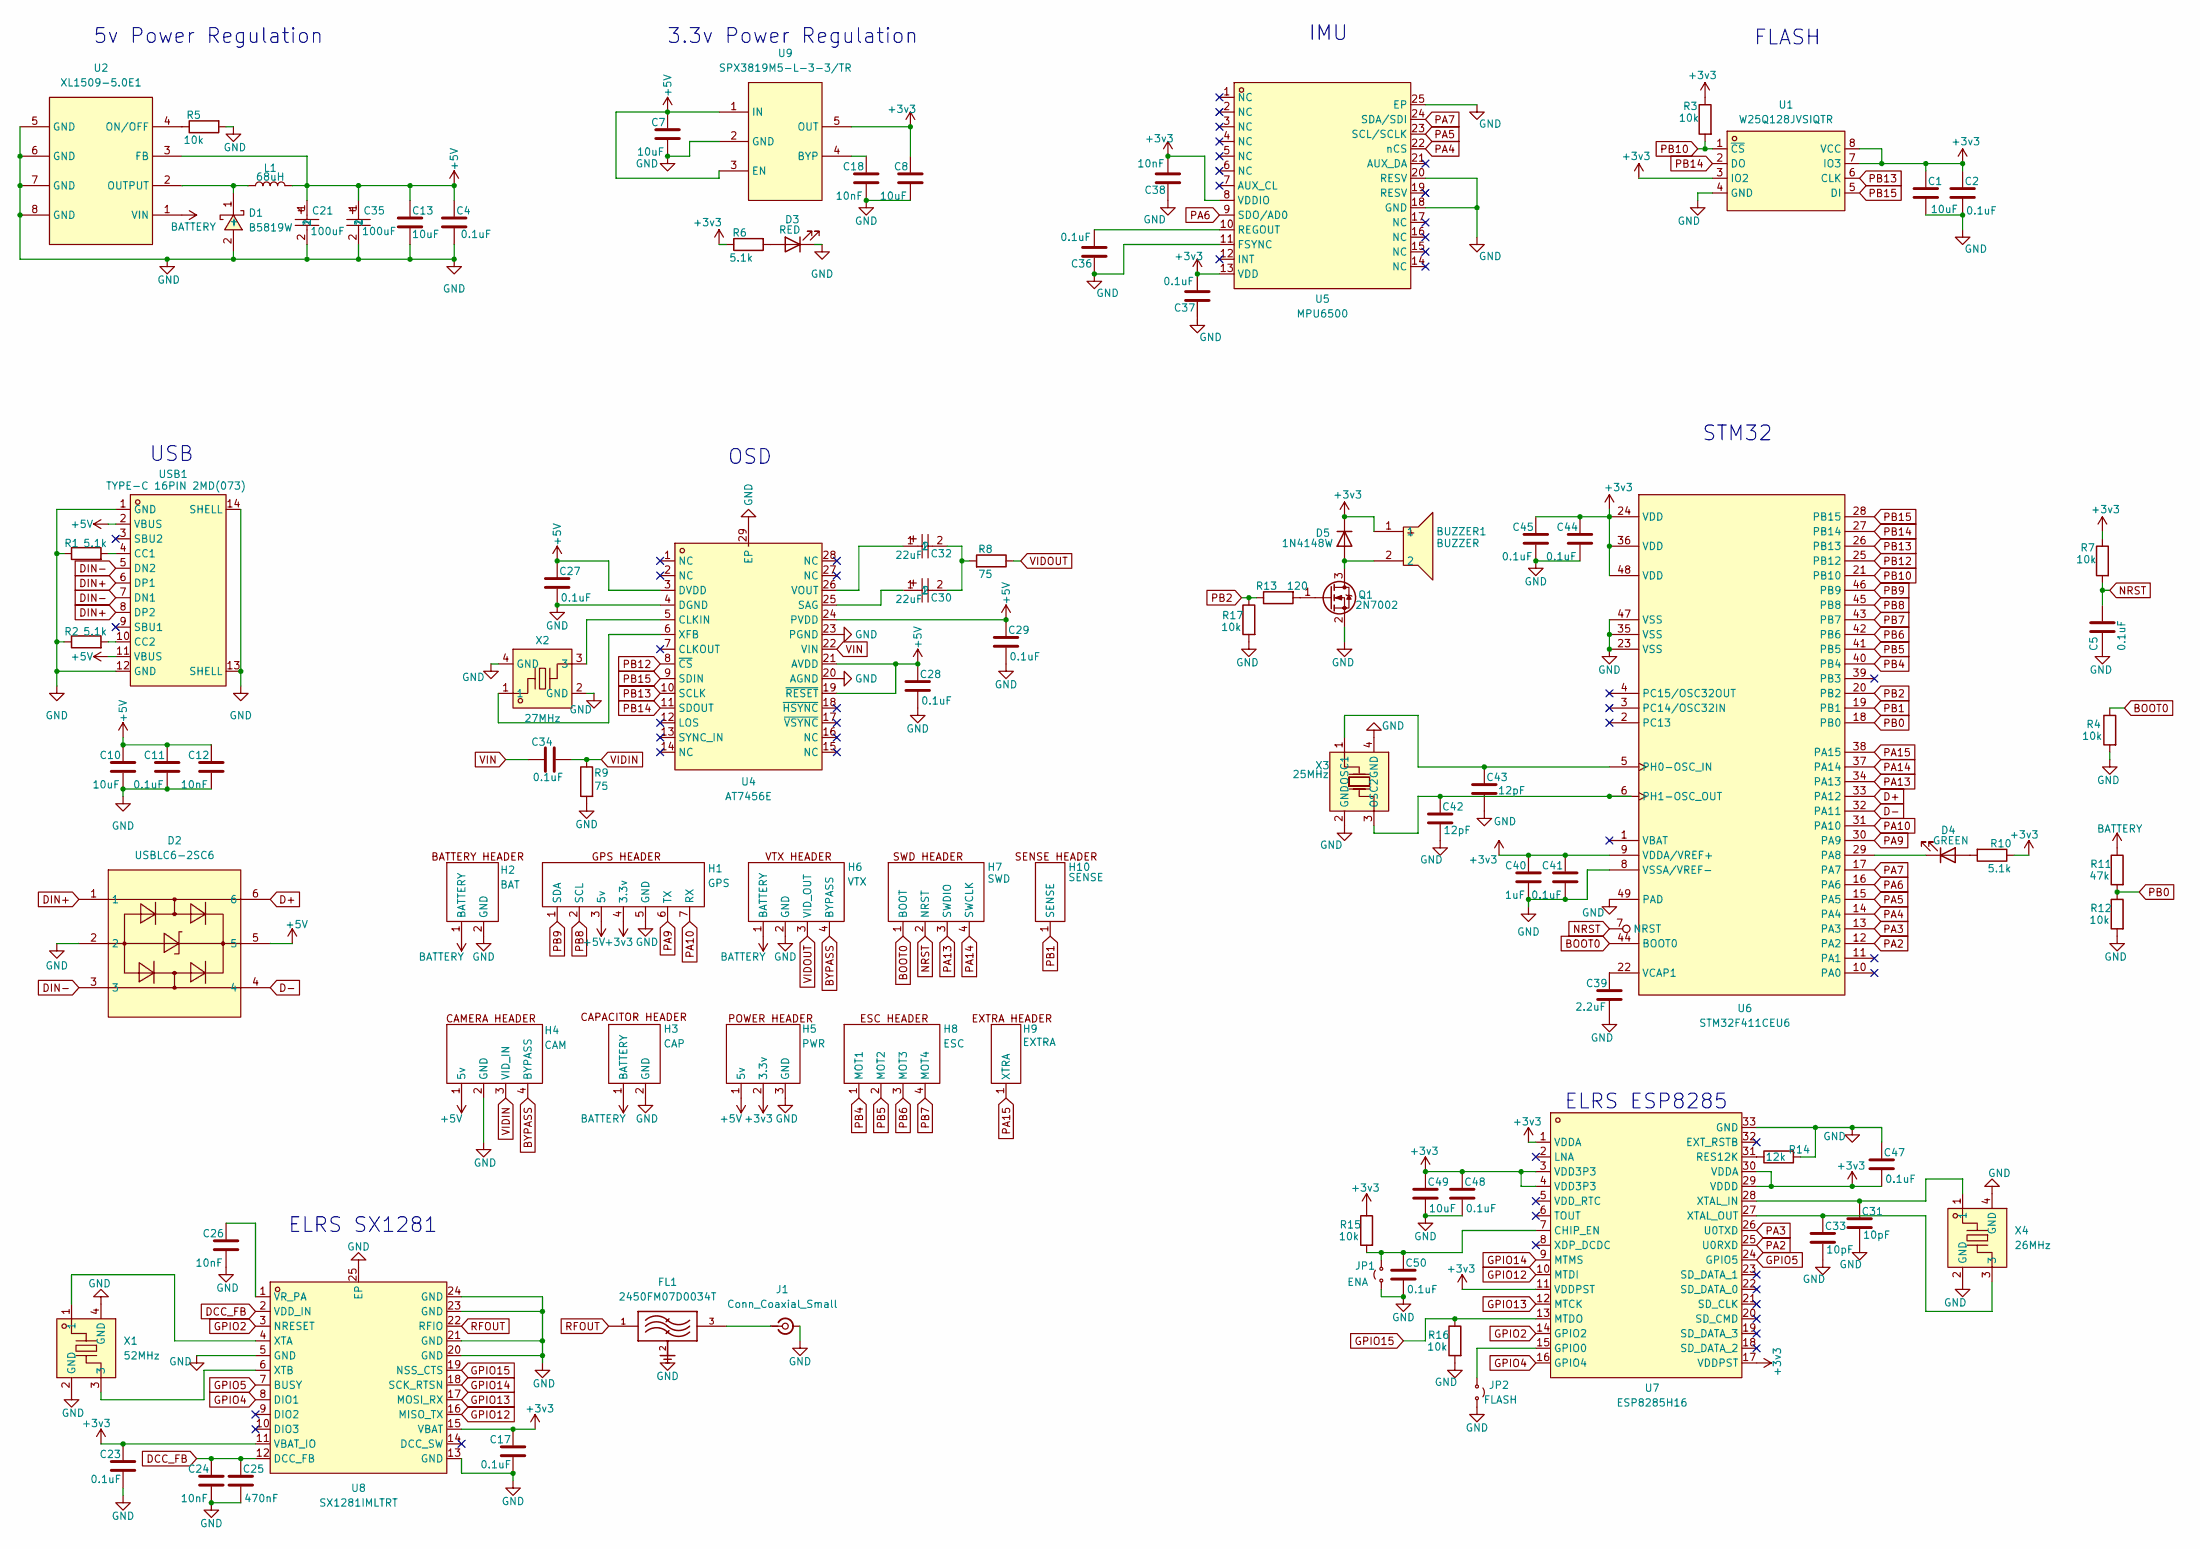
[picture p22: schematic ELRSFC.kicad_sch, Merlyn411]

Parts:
BUZZER1: BUZZER; BUZ-SMD_L9.6-W9.6-LS10.0-R; LCSC Part C96127
C1, C7, C8, C10, C13, C49: 10uF; C_0402_1005Metric; LCSC Part C15525
C2, C4, C11, C17, C23, C27, C28, C29, C34, C36, C37, C41, C44, C45, C47, C48, C50: 0.1uF; C_0402_1005Metric; LCSC Part C307331
C5: 0.1uF; C_0603_1608Metric
C12, C18, C24, C26, C38: 10nF; C_0402_1005Metric; LCSC Part C15195
C21, C35: 100uF; CASE-B_3528; LCSC Part C16133
C25: 470nF; C_0603_1608Metric; LCSC Part C1623
C30, C32: 22uF; CAP-SMD_L3.2-W1.6-RD-C7171
C31, C33: 10pF; C_0402_1005Metric; LCSC Part C32949
C39: 2.2uF; C_0402_1005Metric; LCSC Part C12530
C40: 1uF; C_0402_1005Metric; LCSC Part C52923
C42, C43: 12pF; C_0402_1005Metric; LCSC Part C1547
D1: B5819W; SOD-123_L2.7-W1.6-LS3.7-RD-1; LCSC Part C8598
D2: USBLC6-2SC6; SOT-23-6_L2.9-W1.6-P0.95-LS2.8-BL; LCSC Part C7519
D3: RED; LED_0805_2012Metric; LCSC Part C84256
D4: GREEN; LED_0805_2012Metric; LCSC Part C2297
D5: 1N4148W; D_SOD-123
FL1: 2450FM07D0034T; FIL_2450FM07D0034T; PARTREV 1.2
H1: GPS
H2: BAT
H3: CAP
H4: CAM
H5: PWR
H6: VTX
H7: SWD
H8: ESC
H9: EXTRA
H10: SENSE
J1: Conn_Coaxial_Small; UFL
JP1: ENA
JP2: FLASH
L1: 68uH; L_Sunlord_SWPA8040S
Q1: 2N7002; SOT-23
R1, R2, R6, R10: 5.1k; R_0402_1005Metric; LCSC Part C25905
R3, R5, R12, R15, R16, R17: 10k; R_0402_1005Metric; LCSC Part C25744
R4, R7: 10k; R_0603_1608Metric
R8, R9: 75; R_0603_1608Metric; LCSC Part C4275
R11: 47k; R_0402_1005Metric; LCSC Part C25792
R13: 120; R_0402_1005Metric; LCSC Part C25079
R14: 12k; R_0402_1005Metric; LCSC Part C25752
U1: W25Q128JVSIQTR; SOIC-8_L5.3-W5.3-P1.27-LS8.0-BL; LCSC Part C97521
U2: XL1509-5.0E1; SOIC-8_L5.0-W4.0-P1.27-LS6.0-BL; LCSC Part C61063
U4: AT7456E; TSSOP-28_L9.7-W4.4-P0.65-LS6.4-BL-EP-2; LCSC Part C82351
U5: MPU6500; QFN-24_L3.0-W3.0-P0.40-BL-EP; LCSC Part C50278
U6: STM32F411CEU6; UFQFPN-48_L7.0-W7.0-P0.50-BL-EP; LCSC Part C60420
U7: ESP8285H16; QFN-32_L5.0-W5.0-P0.50-TL-EP3.7; LCSC Part C967019
U8: SX1281IMLTRT; QFN-24_L4.0-W4.0-P0.50-TL-EP2.6; LCSC Part C2151551
U9: SPX3819M5-L-3-3/TR; SOT-23-5_L3.0-W1.7-P0.95-LS2.8-BL; LCSC Part C9055
USB1: TYPE-C 16PIN 2MD(073); USB-C-SMD_TYPE-C-6PIN-2MD-073; LCSC Part C2765186
X1: 52MHz; CRYSTAL-SMD_4P-L2.0-W1.6-BL; LCSC Part C3034316
X2: 27MHz; CRYSTAL-SMD_4P-L2.0-W1.6-BL; LCSC Part C648952
X3: 25MHz; CRYSTAL-SMD_4P-L3.2-W2.5-BL; LCSC Part C9006
X4: 26MHz; CRYSTAL-SMD_4P-L2.0-W1.6-BL; LCSC Part C19272774

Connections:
+3v3: BUZZER1.1, C1.1, C2.1, C8.1, C17.1, C23.1, C37.2, C38.2, C40.1, C41.1, C44.1, C45.1, C47.2, C48.1, C49.1, D5.1 (K), H1.4 (3.3v), H5.2 (3.3v), R3.1, R6.1, R7.1, R10.1, R15.1, U1.3 (IO2), U1.7 (IO3), U1.8 (VCC), U5.8 (VDDIO), U5.13 (VDD), U6.9 (VDDA/VREF+), U6.24 (VDD), U6.36 (VDD), U6.48 (VDD), U7.1 (VDDA), U7.3 (VDD3P3), U7.4 (VDD3P3), U7.11 (VDDPST), U7.17 (VDDPST), U7.29 (VDDD), U7.30 (VDDA), U8.11 (VBAT_IO), U8.15 (VBAT), U9.5 (OUT)
+5V: C4.1, C7.1, C10.1, C11.1, C12.1, C13.1, C21.1, C27.1, C28.1, C29.1, C35.1, D2.5, H1.3 (5v), H4.1 (5v), H5.1 (5v), L1.2, U2.3 (FB), U4.3 (DVDD), U4.19 (~RESET), U4.21 (AVDD), U4.24 (PVDD), U9.1 (IN), U9.3 (EN), USB1.2 (VBUS), USB1.11 (VBUS)
BATTERY: H2.1 (BATTERY), H3.1 (BATTERY), H6.1 (BATTERY), R11.1, U2.1 (VIN)
BOOT0: H7.1 (BOOT), R4.1, U6.44 (BOOT0)
BYPASS: H4.4 (BYPASS), H6.4 (BYPASS)
D+: D2.6, U6.33 (PA12)
D-: D2.4, U6.32 (PA11)
DCC_FB: C24.1, C25.1, U8.2 (VDD_IN), U8.12 (DCC_FB)
DIN+: D2.1, USB1.6 (DP1), USB1.8 (DP2)
DIN-: D2.3, USB1.5 (DN2), USB1.7 (DN1)
GND: C1.2, C2.2, C4.2, C5.1, C7.2, C8.2, C10.2, C11.2, C12.2, C13.2, C17.2, C18.2, C21.2, C23.2, C24.2, C25.2, C26.2, C27.2, C28.2, C29.2, C31.2, C33.2, C35.2, C36.1, C37.1, C38.1, C39.2, C40.2, C41.2, C42.2, C43.2, C44.2, C45.2, C47.1, C48.2, C49.2, C50.2, D1.2 (+), D2.2, D3.1 (K), FL1.2, FL1.4, H1.5 (GND), H2.2 (GND), H3.2 (GND), H4.2 (GND), H5.3 (GND), H6.2 (GND), J1.2 (Ext), JP1.1 (A), JP2.1 (A), Q1.2 (S), R1.1, R2.1, R4.2, R5.2, R9.2, R12.2, R14.2, R16.2, R17.2, U1.4 (GND), U2.5 (GND), U2.6 (GND), U2.7 (GND), U2.8 (GND), U4.4 (DGND), U4.20 (AGND), U4.23 (PGND), U4.29 (EP), U5.11 (FSYNC), U5.18 (GND), U5.20 (RESV), U5.25 (EP), U6.8 (VSSA/VREF-), U6.23 (VSS), U6.35 (VSS), U6.47 (VSS), U6.49 (PAD), U7.33 (GND), U8.5 (GND), U8.13 (GND), U8.20 (GND), U8.21 (GND), U8.23 (GND), U8.24 (GND), U8.25 (EP), U9.2 (GND), USB1.1 (GND), USB1.12 (GND), USB1.13 (SHELL), USB1.14 (SHELL), X1.2 (GND), X1.4 (GND), X2.2 (GND), X2.4 (GND), X3.2 (GND), X3.4 (GND), X4.2 (GND), X4.4 (GND)
GPIO2: U7.14 (GPIO2), U8.3 (NRESET)
GPIO4: U7.16 (GPIO4), U8.8 (DIO1)
GPIO5: U7.24 (GPIO5), U8.7 (BUSY)
GPIO12: U7.10 (MTDI), U8.16 (MISO_TX)
GPIO13: U7.12 (MTCK), U8.17 (MOSI_RX)
GPIO14: U7.9 (MTMS), U8.18 (SCK_RTSN)
GPIO15: R16.1, U7.13 (MTDO), U8.19 (NSS_CTS)
NRST: C5.2, H7.2 (NRST), R7.2, U6.7 (NRST)
unnamed: C30.2, C32.2, R8.2
unnamed: D1.1 (-), L1.1, U2.2 (OUTPUT)
unnamed: D3.2 (A), R6.2
unnamed: D4.2 (A), R10.2
unnamed: D4.1 (K), U6.29 (PA8)
unnamed: BUZZER1.2, D5.2 (A), Q1.3 (D)
unnamed: FL1.3, J1.1 (In)
unnamed: C50.1, JP1.2 (B), R15.2, U7.7 (CHIP_EN)
unnamed: JP2.2 (B), U7.15 (GPIO0)
unnamed: Q1.1 (G), R13.2
unnamed: R5.1, U2.4 (ON/OFF)
unnamed: U4.5 (CLKIN), X2.3
unnamed: C30.1, U4.25 (SAG)
unnamed: C32.1, U4.26 (VOUT)
unnamed: U4.6 (XFB), X2.1
unnamed: C36.2, U5.10 (REGOUT)
unnamed: C43.1, U6.5 (PH0-OSC_IN), X3.1 (OSC1)
unnamed: C42.1, U6.6 (PH1-OSC_OUT), X3.3 (OSC2)
unnamed: C39.1, U6.22 (VCAP1)
unnamed: R14.1, U7.31 (RES12K)
unnamed: C31.1, U7.28 (XTAL_IN), X4.1
unnamed: C33.1, U7.27 (XTAL_OUT), X4.3
unnamed: C26.1, U8.1 (VR_PA)
unnamed: U8.4 (XTA), X1.1
unnamed: U8.6 (XTB), X1.3
unnamed: C18.1, U9.4 (BYP)
unnamed: R1.2, USB1.4 (CC1)
unnamed: R2.2, USB1.10 (CC2)
PA2: U6.12 (PA2), U7.25 (U0RXD)
PA3: U6.13 (PA3), U7.26 (U0TXD)
PA4: U5.22 (nCS), U6.14 (PA4)
PA5: U5.23 (SCL/SCLK), U6.15 (PA5)
PA6: U5.9 (SDO/AD0), U6.16 (PA6)
PA7: U5.24 (SDA/SDI), U6.17 (PA7)
PA9: H1.6 (TX), U6.30 (PA9)
PA10: H1.7 (RX), U6.31 (PA10)
PA13: H7.3 (SWDIO), U6.34 (PA13)
PA14: H7.4 (SWCLK), U6.37 (PA14)
PA15: H9.1 (XTRA), U6.38 (PA15)
PB0: R11.2, R12.1, U6.18 (PB0)
PB1: H10.1 (SENSE), U6.19 (PB1)
PB2: R13.1, R17.1, U6.20 (PB2)
PB4: H8.1 (MOT1), U6.40 (PB4)
PB5: H8.2 (MOT2), U6.41 (PB5)
PB6: H8.3 (MOT3), U6.42 (PB6)
PB7: H8.4 (MOT4), U6.43 (PB7)
PB8: H1.2 (SCL), U6.45 (PB8)
PB9: H1.1 (SDA), U6.46 (PB9)
PB10: R3.2, U1.1 (~CS), U6.21 (PB10)
PB12: U4.8 (~CS), U6.25 (PB12)
PB13: U1.6 (CLK), U4.10 (SCLK), U6.26 (PB13)
PB14: U1.2 (DO), U4.11 (SDOUT), U6.27 (PB14)
PB15: U1.5 (DI), U4.9 (SDIN), U6.28 (PB15)
RFOUT: FL1.1, U8.22 (RFIO)
VIDIN: C34.1, H4.3 (VID_IN), R9.1
VIDOUT: H6.3 (VID_OUT), R8.1
VIN: C34.2, U4.22 (VIN)

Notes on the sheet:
ELRS ESP8285
STM32
3.3v Power Regulation
FLASH
OSD
IMU
USB
5v Power Regulation
ELRS SX1281

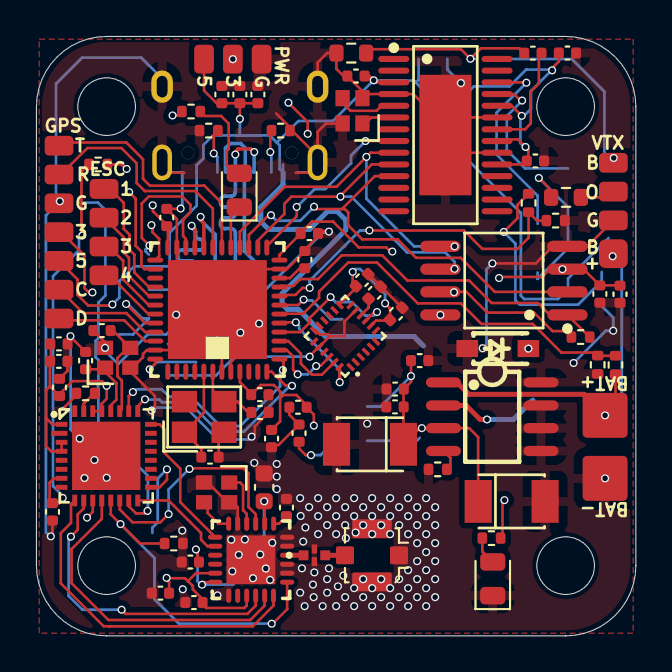
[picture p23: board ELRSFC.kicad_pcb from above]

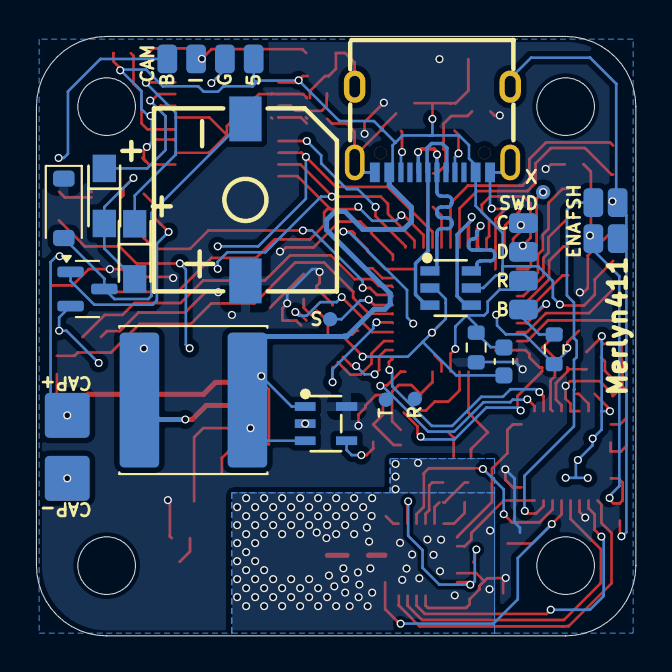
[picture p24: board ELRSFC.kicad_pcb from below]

Board: 2 copper layers, 33.3 x 33.3 mm, 92 parts (19 on the bottom side), 76 nets.

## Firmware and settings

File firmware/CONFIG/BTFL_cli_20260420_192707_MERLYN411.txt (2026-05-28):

# 

# dump

# version
# Betaflight / STM32F411 (F411) 2025.12.2 Apr 20 2026 / 20:58:02 (norevision) MSP API: 1.47
# config rev: e378347

# start the command batch
batch start

board_name MERLYN411
manufacturer_id ANSON

# name: -

# resources
resource BEEPER 1 B02
resource MOTOR 1 B04
resource MOTOR 2 B05
resource MOTOR 3 B06
resource MOTOR 4 B07
resource MOTOR 5 NONE
resource MOTOR 6 NONE
resource MOTOR 7 NONE
resource MOTOR 8 NONE
resource SERVO 1 NONE
resource SERVO 2 NONE
resource SERVO 3 NONE
resource SERVO 4 NONE
resource SERVO 5 NONE
resource SERVO 6 NONE
resource SERVO 7 NONE
resource SERVO 8 NONE
resource PPM 1 NONE
resource PWM 1 NONE
resource PWM 2 NONE
resource PWM 3 NONE
resource PWM 4 NONE
resource PWM 5 NONE
resource PWM 6 NONE
resource PWM 7 NONE
resource PWM 8 NONE
resource SERIAL_TX 1 A09
resource SERIAL_TX 2 A02
resource SERIAL_TX 3 NONE
resource SERIAL_TX 4 NONE
resource SERIAL_TX 5 NONE
resource SERIAL_TX 6 NONE
resource SERIAL_RX 1 A10
resource SERIAL_RX 2 A03
resource SERIAL_RX 3 NONE
resource SERIAL_RX 4 NONE
resource SERIAL_RX 5 NONE
resource SERIAL_RX 6 NONE
resource INVERTER 1 NONE
resource INVERTER 2 NONE
resource INVERTER 3 NONE
resource INVERTER 4 NONE
resource INVERTER 5 NONE
resource INVERTER 6 NONE
resource SOFTSERIAL_TX 1 A15
resource SOFTSERIAL_TX 2 NONE
resource SOFTSERIAL_RX 1 NONE
resource SOFTSERIAL_RX 2 NONE
resource I2C_SCL 1 B08
resource I2C_SCL 2 NONE
resource I2C_SCL 3 NONE
resource I2C_SDA 1 B09
resource I2C_SDA 2 NONE
resource I2C_SDA 3 NONE
resource LED 1 A08
resource LED 2 NONE
resource LED 3 NONE
resource RX_BIND 1 NONE
resource RX_BIND_PLUG 1 NONE
resource SPI_SCK 1 A05
resource SPI_SCK 2 B13
resource SPI_SCK 3 NONE
resource SPI_SDI 1 A06
resource SPI_SDI 2 B14
resource SPI_SDI 3 NONE
resource SPI_SDO 1 A07
resource SPI_SDO 2 B15
resource SPI_SDO 3 NONE
resource ESCSERIAL 1 NONE
resource ADC_BATT 1 B00
resource ADC_RSSI 1 NONE
resource ADC_CURR 1 B01
resource ADC_EXT 1 NONE
resource COMPASS_CS 1 NONE
resource COMPASS_EXTI 1 NONE
resource PINIO 1 NONE
resource PINIO 2 NONE
resource PINIO 3 NONE
resource PINIO 4 NONE
resource USB_MSC_PIN 1 NONE
resource FLASH_CS 1 B10
resource OSD_CS 1 B12
resource GYRO_EXTI 1 NONE
resource GYRO_CS 1 A04
resource USB_DETECT 1 NONE
resource PULLUP 1 NONE
resource PULLUP 2 NONE
resource PULLUP 3 NONE
resource PULLUP 4 NONE
resource PULLDOWN 1 NONE
resource PULLDOWN 2 NONE
resource PULLDOWN 3 NONE
resource PULLDOWN 4 NONE

# timer
timer B04 AF2
# pin B04: TIM3 CH1 (AF2)
timer B05 AF2
# pin B05: TIM3 CH2 (AF2)
timer B06 AF2
# pin B06: TIM4 CH1 (AF2)
timer B07 AF2
# pin B07: TIM4 CH2 (AF2)
timer A15 AF1
# pin A15: TIM2 CH1 (AF1)

# dma
dma SPI_SDO 1 NONE
dma SPI_SDO 2 NONE
dma SPI_SDO 3 NONE
dma SPI_SDI 1 NONE
dma SPI_SDI 2 NONE
dma SPI_SDI 3 NONE
dma SPI_TX 1 NONE
dma SPI_TX 2 NONE
dma SPI_TX 3 NONE
dma SPI_RX 1 NONE
dma SPI_RX 2 NONE
dma SPI_RX 3 NONE
dma ADC 1 1
# ADC 1: DMA2 Stream 4 Channel 0
dma ADC 2 NONE
dma ADC 3 NONE
dma UART_TX 1 NONE
dma UART_TX 2 NONE
dma UART_TX 3 NONE
dma UART_TX 4 NONE
dma UART_TX 5 NONE
dma UART_TX 6 NONE
dma UART_RX 1 NONE
dma UART_RX 2 NONE
dma UART_RX 3 NONE
dma UART_RX 4 NONE
dma UART_RX 5 NONE
dma UART_RX 6 NONE
dma pin B04 0
# pin B04: DMA1 Stream 4 Channel 5
dma pin B05 0
# pin B05: DMA1 Stream 5 Channel 5
dma pin B06 0
# pin B06: DMA1 Stream 0 Channel 2
dma pin B07 0
# pin B07: DMA1 Stream 3 Channel 2
dma pin A15 0
# pin A15: DMA1 Stream 5 Channel 3

# feature
feature -RX_PPM
feature -INFLIGHT_ACC_CAL
feature -RX_SERIAL
feature -MOTOR_STOP
feature -SERVO_TILT
feature -SOFTSERIAL
feature -GPS
feature -OPTICALFLOW
feature -RANGEFINDER
feature -TELEMETRY
feature -3D
feature -RX_PARALLEL_PWM
feature -RSSI_ADC
feature -LED_STRIP
feature -DISPLAY
feature -OSD
feature -CHANNEL_FORWARDING
feature -TRANSPONDER
feature -AIRMODE
feature -RX_SPI
feature -ESC_SENSOR
feature -ANTI_GRAVITY
feature RX_SERIAL
feature SOFTSERIAL
feature GPS
feature TELEMETRY
feature OSD
feature AIRMODE
feature ANTI_GRAVITY

# serial
serial VCP 1 115200 57600 0 115200
serial UART1 2 115200 57600 0 115200
serial UART2 64 115200 115200 0 115200
serial SOFT1 8192 115200 19200 0 19200

# mixer
mixer QUADX

mmix reset


# servo
servo 0 1000 2000 1500 100 -1
servo 1 1000 2000 1500 100 -1
servo 2 1000 2000 1500 100 -1
servo 3 1000 2000 1500 100 -1
servo 4 1000 2000 1500 100 -1
servo 5 1000 2000 1500 100 -1
servo 6 1000 2000 1500 100 -1
servo 7 1000 2000 1500 100 -1

# servo mixer
smix reset


# beeper
beeper GYRO_CALIBRATED
beeper -RX_LOST
beeper RX_LOST_LANDING
beeper -DISARMING
beeper ARMING
beeper ARMING_GPS_FIX
beeper ARMING_GPS_NO_FIX
beeper -BAT_CRIT_LOW
beeper -BAT_LOW
beeper -GPS_STATUS
beeper RX_SET
beeper ACC_CALIBRATION
beeper ACC_CALIBRATION_FAIL
beeper READY_BEEP
beeper MULTI_BEEPS
beeper DISARM_REPEAT
beeper ARMED
beeper SYSTEM_INIT
beeper -ON_USB
beeper BLACKBOX_ERASE
beeper CRASHFLIP
beeper CAM_CONNECTION_OPEN
beeper CAM_CONNECTION_CLOSE

# beacon
beacon -RX_LOST
beacon -RX_SET

# map
map AETR1234

# aux
aux 0 0 0 1975 2025 0 0
aux 1 1 1 1475 1525 0 0
aux 2 2 1 1975 2025 0 0
aux 3 46 2 1975 2025 0 0
aux 4 13 5 1975 2025 0 0
aux 5 19 4 1650 2025 0 0
aux 6 35 3 1975 2025 0 0
aux 7 0 0 900 900 0 0
aux 8 0 0 900 900 0 0
aux 9 0 0 900 900 0 0
aux 10 0 0 900 900 0 0
aux 11 0 0 900 900 0 0
aux 12 0 0 900 900 0 0
aux 13 0 0 900 900 0 0
aux 14 0 0 900 900 0 0
aux 15 0 0 900 900 0 0
aux 16 0 0 900 900 0 0
aux 17 0 0 900 900 0 0
aux 18 0 0 900 900 0 0
aux 19 0 0 900 900 0 0

# adjrange
adjrange 0 0 0 900 900 0 0 0 0
adjrange 1 0 0 900 900 0 0 0 0
adjrange 2 0 0 900 900 0 0 0 0
adjrange 3 0 0 900 900 0 0 0 0
adjrange 4 0 0 900 900 0 0 0 0
adjrange 5 0 0 900 900 0 0 0 0
adjrange 6 0 0 900 900 0 0 0 0
adjrange 7 0 0 900 900 0 0 0 0
adjrange 8 0 0 900 900 0 0 0 0
adjrange 9 0 0 900 900 0 0 0 0
adjrange 10 0 0 900 900 0 0 0 0
adjrange 11 0 0 900 900 0 0 0 0
adjrange 12 0 0 900 900 0 0 0 0
adjrange 13 0 0 900 900 0 0 0 0
adjrange 14 0 0 900 900 0 0 0 0
adjrange 15 0 0 900 900 0 0 0 0
adjrange 16 0 0 900 900 0 0 0 0
adjrange 17 0 0 900 900 0 0 0 0
adjrange 18 0 0 900 900 0 0 0 0
adjrange 19 0 0 900 900 0 0 0 0
adjrange 20 0 0 900 900 0 0 0 0
adjrange 21 0 0 900 900 0 0 0 0
adjrange 22 0 0 900 900 0 0 0 0
adjrange 23 0 0 900 900 0 0 0 0
adjrange 24 0 0 900 900 0 0 0 0
adjrange 25 0 0 900 900 0 0 0 0
adjrange 26 0 0 900 900 0 0 0 0
adjrange 27 0 0 900 900 0 0 0 0
adjrange 28 0 0 900 900 0 0 0 0
adjrange 29 0 0 900 900 0 0 0 0

# rxrange
rxrange 0 1000 2000
rxrange 1 1000 2000
rxrange 2 1000 2000
rxrange 3 1000 2000

# vtxtable
vtxtable bands 5
vtxtable channels 8
vtxtable band 1 BOSCAM_A A CUSTOM  5865 5845 5825 5805 5785 5765 5745 5725
vtxtable band 2 BOSCAM_B B CUSTOM  5733 5752 5771 5790 5809 5828 5847 5866
vtxtable band 3 BOSCAM_E E CUSTOM  5705 5685 5665 5645 5885 5905 5925 5945
vtxtable band 4 FATSHARK F CUSTOM  5740 5760 5780 5800 5820 5840 5860 5880
vtxtable band 5 RACEBAND R CUSTOM  5658 5695 5732 5769 5806 5843 5880 5917
vtxtable powerlevels 5
vtxtable powervalues 25 100 200 400 600
vtxtable powerlabels 25 100 200 400 600

# vtx
vtx 0 0 0 0 0 900 900
vtx 1 0 0 0 0 900 900
vtx 2 0 0 0 0 900 900
vtx 3 0 0 0 0 900 900
vtx 4 0 0 0 0 900 900
vtx 5 0 0 0 0 900 900
vtx 6 0 0 0 0 900 900
vtx 7 0 0 0 0 900 900
vtx 8 0 0 0 0 900 900
vtx 9 0 0 0 0 900 900

# rxfail
rxfail 0 a
rxfail 1 a
rxfail 2 a
rxfail 3 s 1500
rxfail 4 h
rxfail 5 s 1500
rxfail 6 h
rxfail 7 h
rxfail 8 h
rxfail 9 h
rxfail 10 h
rxfail 11 h
rxfail 12 h
rxfail 13 h
rxfail 14 h
rxfail 15 h
rxfail 16 h
rxfail 17 h
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

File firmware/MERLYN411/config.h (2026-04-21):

/*
 * This file is part of Betaflight.
 *
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
 * See the GNU General Public License for more details.
 *
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
 * If not, see <http://www.gnu.org/licenses/>.
 */

#pragma once

#define FC_TARGET_MCU      STM32F411

#define BOARD_NAME         MERLYN411
#define MANUFACTURER_ID    ANSON

// ---- INTERNAL COMPONENTS ----
#define USE_ACC
#define USE_ACC_MPU6500
#define USE_ACC_SPI_MPU6500

#define USE_GYRO
#define USE_GYRO_MPU6500
#define USE_GYRO_SPI_MPU6500

#define USE_MAX7456

#define USE_FLASH
#define USE_FLASH_W25Q128FV

// ---- EXTERNAL CONNECTABLE COMPONENTS ---
#define USE_MAG
#define USE_MAG_AK8963
#define USE_MAG_AK8975
#define USE_MAG_HMC5883
#define USE_MAG_IST8310
#define USE_MAG_LIS2MDL
#define USE_MAG_LIS3MDL
#define USE_MAG_QMC5883
#define USE_MPU9250_MAG
#define USE_MAG_MPU925X_AK8963

#define USE_GPS
#define USE_RANGEFINDER
#define USE_ALTITUDE_HOLD
#define USE_POSITION_HOLD

#define USE_TELEMETRY
#define USE_TELEMETRY_LTM
#define USE_TELEMETRY_CRSF
#define USE_TELEMETRY_GHST
#define USE_TELEMETRY_HOTT
#define USE_TELEMETRY_IBUS
#define USE_TELEMETRY_SRXL
#define USE_TELEMETRY_MAVLINK
#define USE_TELEMETRY_SMARTPORT
#define USE_TELEMETRY_FRSKY_HUB
#define USE_TELEMETRY_IBUS_EXTENDED

// ---- PIN MAPPING ----
#define LED0_PIN             PA8

#define ADC_VBAT_PIN         PB0
#define ADC_CURR_PIN         PB1
#define BEEPER_PIN           PB2
#define BEEPER_INVERTED

#define MOTOR1_PIN           PB4
#define MOTOR2_PIN           PB5
#define MOTOR3_PIN           PB6
#define MOTOR4_PIN           PB7

#define UART1_TX_PIN         PA9
#define UART1_RX_PIN         PA10
#define UART2_TX_PIN         PA2
#define UART2_RX_PIN         PA3

#define USE_SOFTSERIAL
#define USE_SOFTSERIAL1
#define SOFTSERIAL1_TX_PIN   PA15

#define I2C1_SCL_PIN         PB8
#define I2C1_SDA_PIN         PB9

#define SPI1_SCK_PIN         PA5
#define SPI1_SDI_PIN         PA6
#define SPI1_SDO_PIN         PA7

#define SPI2_SCK_PIN         PB13
#define SPI2_SDI_PIN         PB14
#define SPI2_SDO_PIN         PB15

#define GYRO_1_CS_PIN        PA4
#define FLASH_CS_PIN         PB10
#define MAX7456_SPI_CS_PIN   PB12

// ---- TIMER MAPPING ----
#define TIMER_PIN_MAPPING \
    TIMER_PIN_MAP( 1, PB4 , 1,  0) \
    TIMER_PIN_MAP( 2, PB5 , 1,  0) \
    TIMER_PIN_MAP( 3, PB6 , 1,  0) \
    TIMER_PIN_MAP( 4, PB7 , 1,  0) \
    TIMER_PIN_MAP( 5, PA15, 1,  0)

// ---- HARDWARE INSTANCES ----
#define ADC1_DMA_OPT         1
#define MAG_I2C_INSTANCE     (I2CDEV_1)
#define BARO_I2C_INSTANCE    (I2CDEV_1)
#define GYRO_1_SPI_INSTANCE  SPI1
#define FLASH_SPI_INSTANCE   SPI2
#define MAX7456_SPI_INSTANCE SPI2
#define SYSTEM_HSE_MHZ       25

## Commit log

2026-03-21 Third journal entry
    [ELRSFC.kicad_pcb, ELRSFC.kicad_sch]
2026-03-22 Fourth journal entry
    [ELRSFC.kicad_sch]
2026-03-22 Fifth journal entry
    [ELRSFC.kicad_sch]
2026-03-23 Sixth entry
    [ELRSFC.kicad_pcb, ELRSFC.kicad_sch, bom.csv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]
2026-03-23 Seventh entry
    [ELRSFC.kicad_pcb, ELRSFC.kicad_sch]
2026-03-24 Eight entry
    [ELRSFC.kicad_pcb, ELRSFC.kicad_sch]
2026-03-25 Ninth entry
    [ELRSFC.kicad_pcb, ELRSFC.kicad_sch]
2026-03-27 high cortisol
    [ELRSFC.kicad_pcb, ELRSFC.kicad_sch]
2026-03-29 (hopefully) finalized PCB
    [ELRSFC.kicad_pcb, ELRSFC.kicad_sch, bom.csv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]
2026-03-31 Almost finalized
    [ELRSFC.kicad_pcb, ELRSFC.kicad_sch, MerlynFPVFrame.f3d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]
2026-03-31 final. Hopefully. The last commit required to fix anything
    [bom.csv]
2026-03-31 whoops added warning about imu orientation
2026-04-01 Added 0.15mm board size on each edge for v cut clearance
    [ELRSFC.kicad_pcb]
2026-04-09 Updated screw and nut hole dimensions
    [camShockMountMoldBottom.stl, camShockMountMoldTop.stl, leftCameraFrame.stl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]
2026-04-14 Updated frame to fit VTX antenna, cutout for GPS, fix readme typo
    [topFrame.stl]
2026-04-16 Enabled softserial, uploaded recommended config
    [BTFL_cli_20260416_205032_MERLYN411.txt]
2026-04-16 FIX Enabled softserial, updated to betaflight 2025.12.2, uploaded recommended config
    [BTFL_cli_20260416_205032_MERLYN411.txt]
2026-04-16 FIX config
    [BTFL_cli_20260416_205032_MERLYN411.txt]
2026-04-21 Fixed buzzer configuration, updated firmware config.h and hex for fixes, updated ideal settings file, uploaded gps config file, updated 3d models
    [BTFL_cli_20260416_205032_MERLYN411.txt, BTFL_cli_20260420_192707_MERLYN411.txt, boardAdapter.stl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]
2026-05-28 Updated GPS and betaflight config, reinforced drone frame and made it work for 2.5" instead of 3" props
    [BTFL_cli_20260420_192707_MERLYN411.txt, leftCameraFrame.stl, leftCameraFrameReinforced.stl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]

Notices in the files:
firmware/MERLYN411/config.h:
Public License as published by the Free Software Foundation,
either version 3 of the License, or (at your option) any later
